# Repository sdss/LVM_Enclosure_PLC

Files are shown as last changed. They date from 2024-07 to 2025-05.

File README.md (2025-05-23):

# LVM_Enclosure_PLC
LVM enclosure PLC code and documentation. There is also an HVAC Modbus configuration file that details the commands to the HVAC system attached to the north side of the attic.

# Where to start?
Generally, look in the Documentation Directory.

# If changes are made

If PLC code is changed then one must
- Upload a new version of the code to PLC code
- Change PLC code.pdf in Documentaiton
- Change PLC Variables.xlsx in Documentation
- Make new state diagrams and upload to PLC State Diagrams

If Hardware is changed
- Change the Altium Schematics
- Upload new PDFs to Documentation

# Branches
* Main: Code deployed on the PLC.

PLC code has been written using Do-more Designer 2.9.

Documentation has the state diagrams for the different subsystems and a variable spreadsheet explaining the variables used in the code.

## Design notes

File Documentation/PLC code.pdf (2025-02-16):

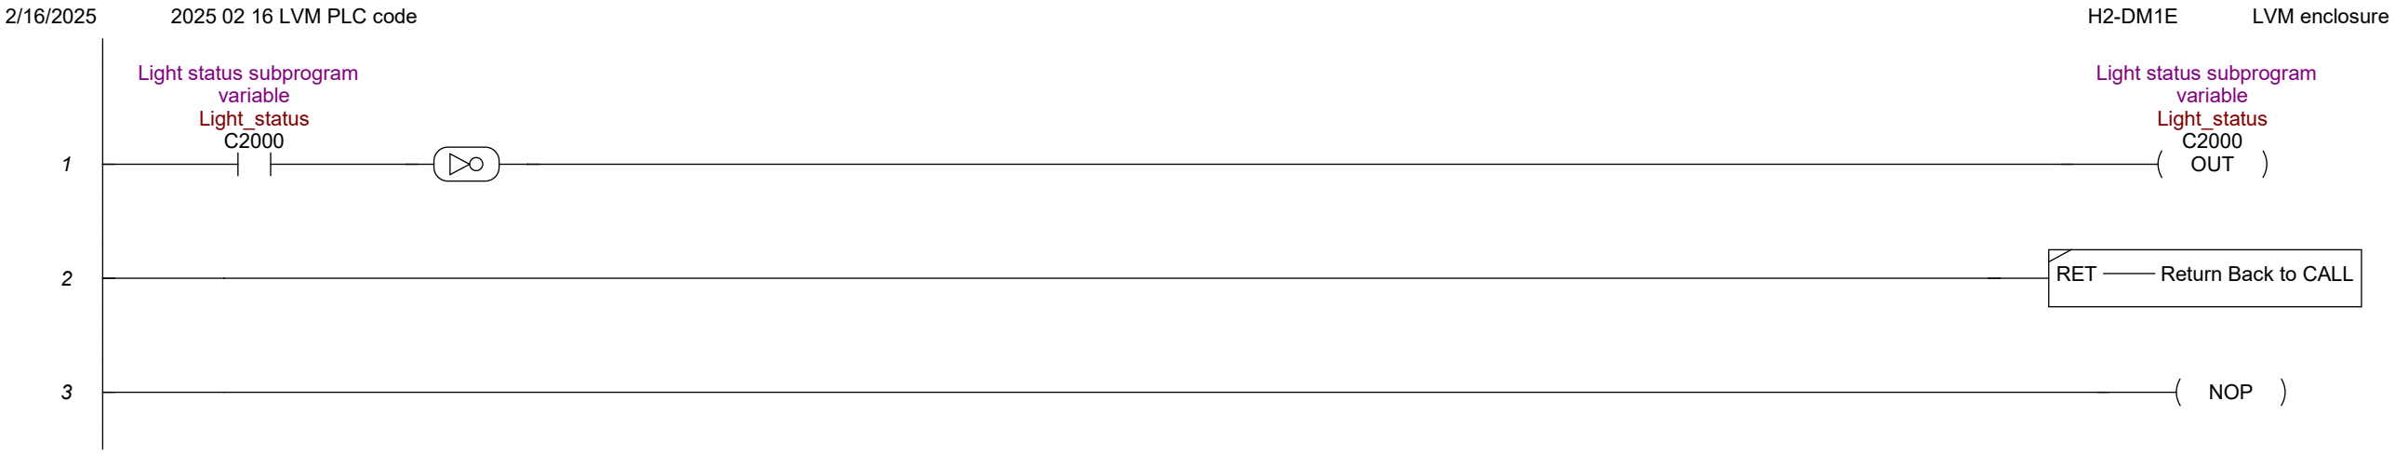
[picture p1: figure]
Light status subprogram variable Light_status C2000; OUT; RET; Return Back to CALL; 3 NOP

2/16/2025 | 2025 02 16 LVM PLC code | H2-DM1E | LVM enclosure
Page 1 | Lights

2/16/2025 | 2025 02 16 LVM PLC code | H2-DM1E | LVM enclosure 1

$FirstScan
ST0

$On
ST1 | INIT | Initialize Data
Start | End | Value
Overcurrent_lim | 75
Dome_move_tout | 165000
curr_delay_val | 2000
Dome_enable

0
Motor_dir

1
HB_error_count

0
Remote_estop

0
Remote_estop_rel

0
date.Date | $Now.Date
date.Time | $Now.Time
UTC | $UTC
C0

0
Rain_mod

0
Rain_el_time

0
No_rain_cdown

0
Drive_speed_a | 100
Drive_speed_b | 70
Roof_logic_sel

1
Rolloff_lout Drive_err_rst_mo

0
Tout_open | 81000
Tout_open_aprch | 37000
Topen_apr | 28000
Tclose | 74000
Tout_close_apr | 44000

Control room lights current sensor input
Local S1:iPT8
Ctl_lights_in
X24
CALL | Call Subroutine
Subroutine | Lights
Optional Input Parameters # | Input Value | Into Subroutine | Count 1 | Ctl_lights_out | Light_status | 1
Optional Output Parameters # | Out of Subroutine | Into | Count 1 | Light_status | Ctl_lights_out | 1

Utilities room lights current sensor input
Local S1:iPT9
Utl_room_in
X25
CALL | Call Subroutine
Subroutine | Lights
Optional Input Parameters # | Input Value | Into Subroutine | Count 1 | Utl_lights_out | Light_status | 1
Optional Output Parameters # | Out of Subroutine | Into | Count 1 | Light_status | Utl_lights_out | 1
Page 2 | $Main

Spectrograph room lights
current sensor input
Local S1:iPT10
Spec_lights_in
X26
CALL | Call Subroutine
Subroutine | Lights
Optional Input Parameters # | Input Value | Into Subroutine | Count 1 | Spec_lights_out | Light_status | 1
Optional Output Parameters # Out of Subroutine | Into | Count 1 | Light_status | Spec_lights_out | 1

Mezzanine lights current
sensor input
Local S1:iPT11
Mze_lights_in
X27
CALL | Call Subroutine
Subroutine | Lights
Optional Input Parameters # | Input Value | Into Subroutine | Count 1 | Mze_lights_out | Light_status | 1
Optional Output Parameters # Out of Subroutine | Into | Count 1 | Light_status | Mze_lights_out | 1

Platform white light
current sensor input
Local S1:iPT12
Plat_Wlights_in
X28
CALL | Call Subroutine
Subroutine | Lights
Optional Input Parameters # | Input Value | Into Subroutine | Count 1 Plat_Wlight_out | Light_status | 1
Optional Output Parameters # Out of Subroutine | Into | Count 1 | Light_status | Plat_Wlight_out | 1

Platform red light current sensor input
Local S1:iPT13
Plat_Rlights_in
X29
CALL | Call Subroutine
Subroutine | Lights
Optional Input Parameters # | Input Value | Into Subroutine | Count 1 | Plat_Rlight_out | Light_status | 1
Optional Output Parameters # Out of Subroutine | Into | Count 1 | Light_status | Plat_Rlight_out | 1

Read GS3 drive Elements using the cpu rs-232 port

Page 3 | $Main

Modbus Address 4… + offset value entered below

Modbus Address 4… + offset value entered below

Copy the encoder counts output to MHR150

- If motor is not moving, send data every minute.
- If motor is moving, send data every second.

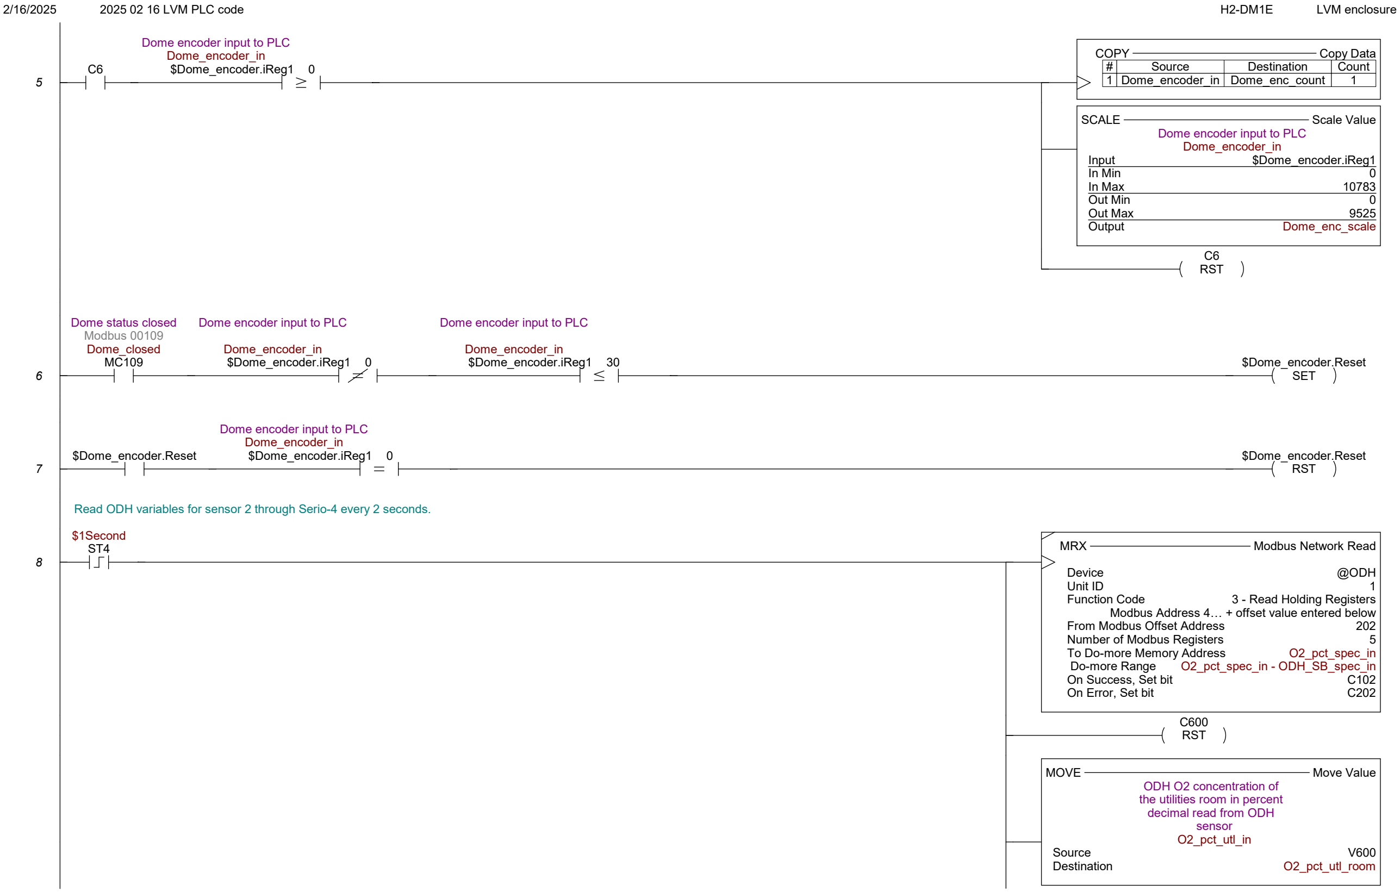
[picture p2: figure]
Dome encoder input to PLC Dome_encoder_in $Dome_encoder.iReg1 0; COPY; Copy Data; Source; Destination; Count; 1 Dome_encoder_in Dome_enc_count; SCALE; Scale Value; Dome encoder input to PLC Dome_encoder_in; Input; $Dome_encoder.iReg1; In Min; In Max; Out Min; Out Max; Output; Dome_enc_scale; RST; Dome status closed Modbus 00109 Dome_closed MC109; Dome encoder input to PLC; Dome_encoder_in $Dome_encoder.iReg1 0; Dome_encoder_in $Dome_encoder.iReg1 30; SET; $Dome_encoder.Reset; $1Second; MRX; Modbus Network Read; Device; @ODH; Unit ID; Function Code; 3 - Read Holding Registers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

Read ODH variables for sensor 2 through Serio-4 every 2 seconds.

Modbus Address 4… + offset value entered below

Page 5 | $Main

MOVE | Move Value
| ODH error code utilities
| room read from ODH sensor
ODH_EC_utl_in
Source | V603
Destination | ODH_EC_utl_room
MOVE | Move Value
| ODH status byte utilities
room, read from ODH
sensor
ODH_SB_utl_in
Source | V604
Destination | ODH_SB_utl_room

9

Read ODH variables for sensor 1 through Serio-4 every 2 seconds.

$1Second
ST4 | MRX | Modbus Network Read
| Device | @ODH
| Unit ID | 1
| Function Code
Modbus Address 4… + offset value entered below
| | 3 - Read Holding Registers
| From Modbus Offset Address | 102
| Number of Modbus Registers | 5
To Do-more Memory Address
| Do-more Range | O2_pct_utl_in - ODH_SB_utl_in O2_pct_utl_in
| On Success, Set bit | C103
| On Error, Set bit | C203

SET

C600

MOVE | Move Value
| ODH O2 concentration of
| the spectrograph room in
| percent decimal, read from
| ODH sensor
| O2_pct_spec_in
Source | V605
Destination | O2_pct_spec_room
MOVE | Move Value
| ODH error code
| spectrograph room, read
| from ODH sensor
| ODH_EC_spec_in
Source | V608
Destination | ODH_EC_spec_room
MOVE | Move Value
| ODH status byte
| spectrograph room, read
| from ODH sensor
| ODH_SB_spec_in
Source | V609
Destination | ODH_SB_spec_room
Page 6 | $Main

10

$1Second
ST4
MATH | Calculate Expression
| Modbus 40700
| Rain_el_time
Result | MHR700
Expression TRUNC(Rain_elapsd_time.Acc / 1000)
MATH | Calculate Expression
| Countdown from 15 min with
no rain
| Modbus 40701
| No_rain_cdown
Result | MHR701
Expression TRUNC(Rain_time.Acc / 1000)

11

$On
ST1

Dome movement mode
selector: selects between
normal operation and
overcurrent only mode.
Modbus 00099
Dome_move_sel
MC99
RUN | Run Program

Overcurrent Drive mode

Program | Drive_overcur
HALT | Halt Program or Task
Code Block | Drive

Dome movement mode
selector: selects between
normal operation and
overcurrent only mode.
Modbus 00099
Dome_move_sel
MC99
RUN | Run Program
Program | Drive
HALT | Halt Program or Task
Overcurrent Drive mode
Code Block Drive_overcur

12

$On
ST1
RUN | Run Program
Rain sensor program
Program | Rain
RUN | Run Program
Program | NTP
RUN | Run Program
Program | Heartbeat
Page 7 | $Main

Optional Output Parameters # Out of Subroutine | Into | Count 1 | Light_status | Ctl_lights_out | 1

18

Modbus utilities room lights toggle
Modbus 00236
UTL_room_tog
MC236
CALL | Call Subroutine
Subroutine | Lights
Optional Input Parameters # | Input Value | Into Subroutine | Count 1 Utl_lights_out | Light_status | 1
Optional Output Parameters # Out of Subroutine | Into | Count 1 | Light_status | Utl_lights_out | 1

RST

Modbus utilities room lights
toggle
Modbus 00236
UTL_room_tog
MC236

19

Utilities room lights current sensor input
Local S1:iPT9
Utl_room_in
X25
OUT

Modbus utilities room lights status
Modbus 00336
UTL_room_stat
MC336

20

Modbus Spectrograph room
lights toggle
Modbus 00237
Spec_room_tog
MC237
CALL | Call Subroutine
Subroutine | Lights
Optional Input Parameters # | Input Value | Into Subroutine | Count 1 Spec_lights_out | Light_status | 1
Optional Output Parameters # Out of Subroutine | Into | Count 1 | Light_status | Spec_lights_out | 1
COPY | Copy Data # | Source | Destination | Count 1 | $UTC | UTC | 1

RST

C0

RST

Modbus Spectrograph room
lights toggle
Modbus 00237
Spec_room_tog
MC237
Page 9 | $Main

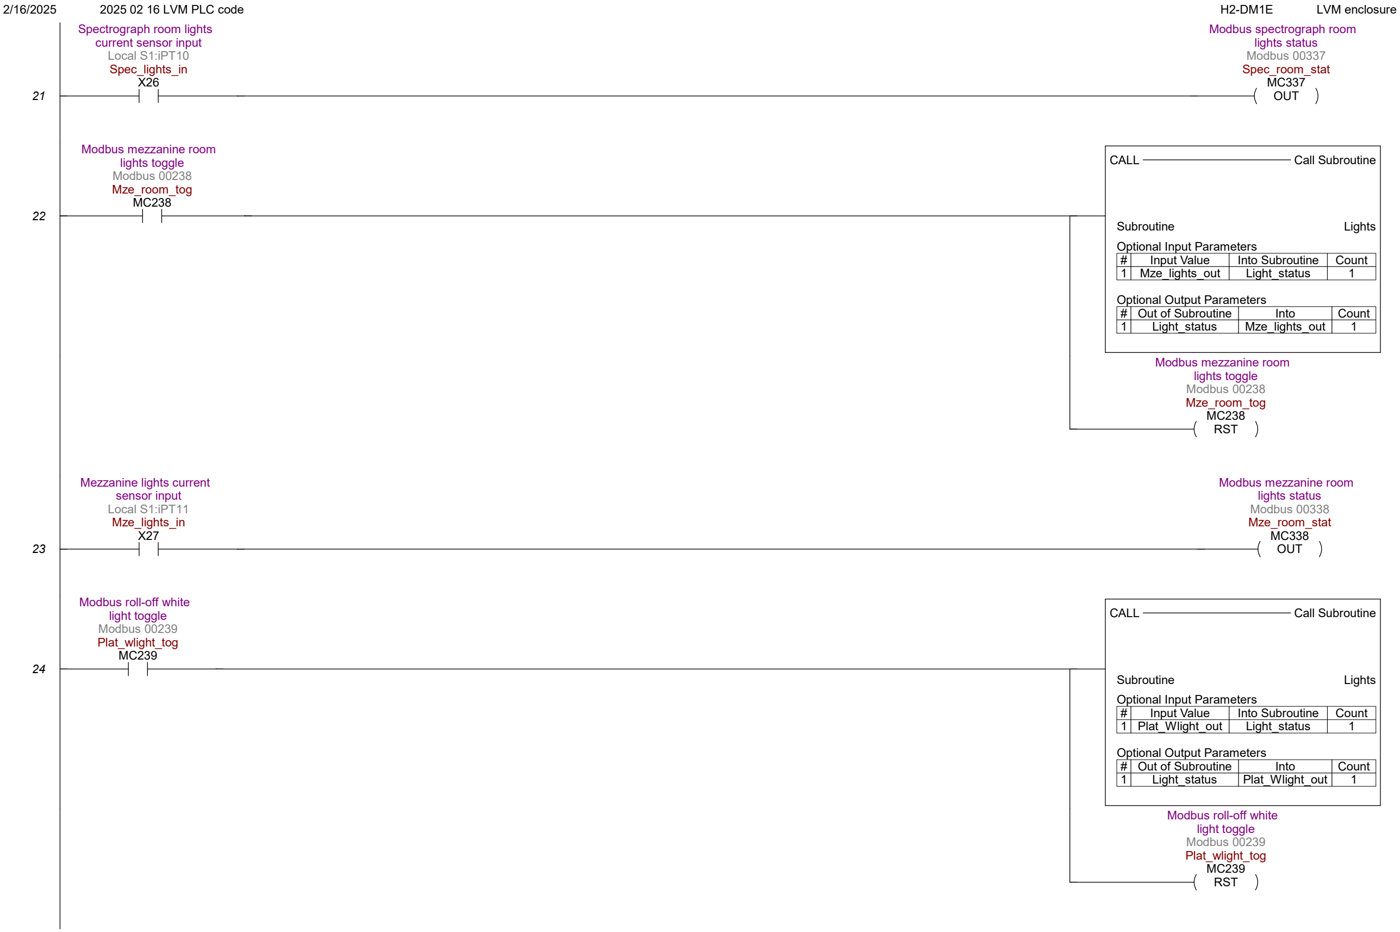
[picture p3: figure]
Spectrograph room lights current sensor input Local S1:iPT10 Spec_lights_in X26; OUT; Modbus spectrograph room lights status Modbus 00337 Spec_room_stat MC337; Modbus mezzanine room lights toggle Modbus 00238 Mze_room_tog MC238; CALL; Call Subroutine; Subroutine; Lights; Optional Input Parameters #; Input Value; Into Subroutine; Count 1 Mze_lights_out; Light_status; RST; Mezzanine lights current sensor input Local S1:iPT11 Mze_lights_in X27; Modbus mezzanine room lights status Modbus 00338 Mze_room_stat MC338; Modbus roll-off white light toggle Modbus 00239 Plat_wlight_tog MC239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

Optional Output Parameters # Out of Subroutine | Into | Count 1 | Light_status | Mze_lights_out | 1
Optional Output Parameters # Out of Subroutine | Into | Count 1 | Light_status | Plat_Wlight_out | 1
Page 10 | $Main

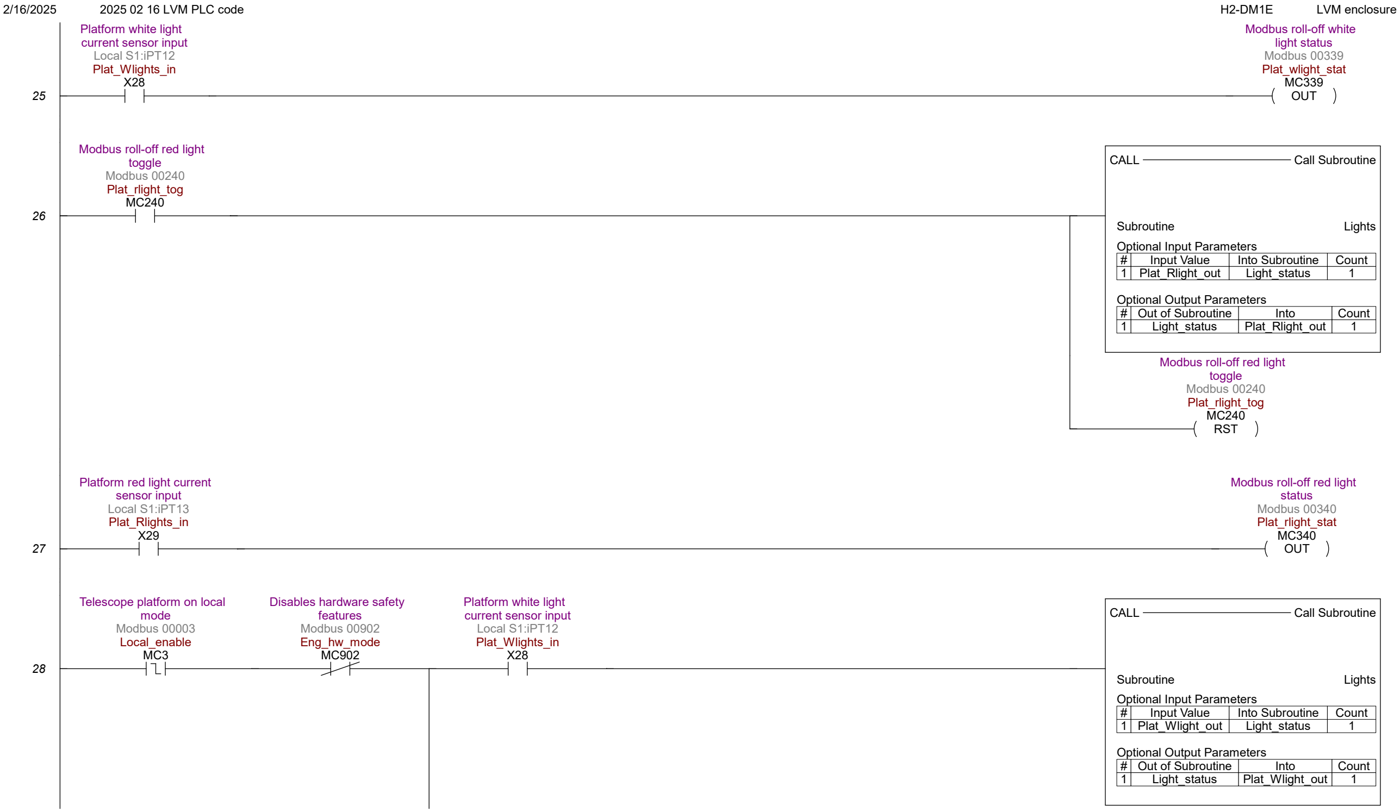
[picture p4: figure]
Platform white light current sensor input Local S1:iPT12 Plat_Wlights_in X28; OUT; Modbus roll-off white light status Modbus 00339 Plat_wlight_stat MC339; Modbus roll-off red light toggle Modbus 00240 Plat_rlight_tog MC240; CALL; Call Subroutine; Subroutine; Lights; Optional Input Parameters; Input Value; Into Subroutine; Count; 1 Plat_Rlight_out; Light_status; Optional Output Parameters; # Out of Subroutine; Into; Plat_Rlight_out; RST; Platform red light current sensor input Local S1:iPT13 Plat_Rlights_in X29; Modbus roll-off red light status Modbus 00340 Plat_rlight_stat MC340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

Page 11 | $Main

Page 12 | $Main

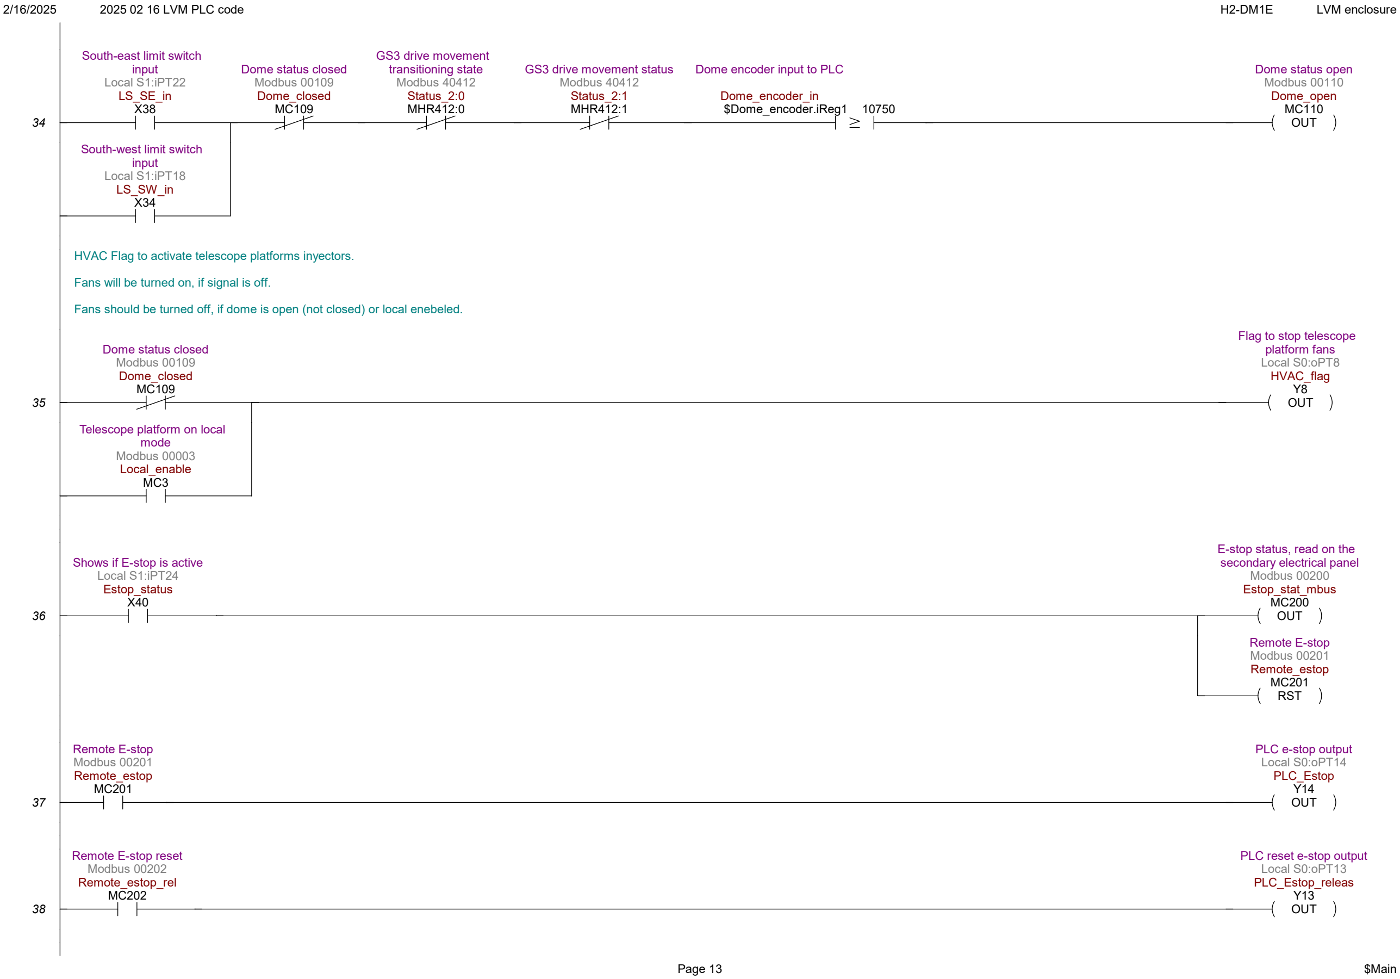
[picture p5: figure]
South-east limit switch input Local S1:iPT22 LS_SE_in X38; Dome status closed Modbus 00109 Dome_closed MC109; GS3 drive movement transitioning state Modbus 40412 Status_2:0 MHR412:0; GS3 drive movement status Modbus 40412 Status_2:1 MHR412:1; Dome encoder input to PLC; Dome_encoder_in $Dome_encoder.iReg1 10750; OUT; Dome status open Modbus 00110 Dome_open MC110; South-west limit switch input Local S1:iPT18 LS_SW_in X34; Flag to stop telescope platform fans Local S0:oPT8 HVAC_flag Y8; Telescope platform on local mode Modbus 00003 Local_enable MC3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

HVAC Flag to activate telescope platforms inyectors.

Fans will be turned on, if signal is off.

Fans should be turned off, if dome is open (not closed) or local enebeled.

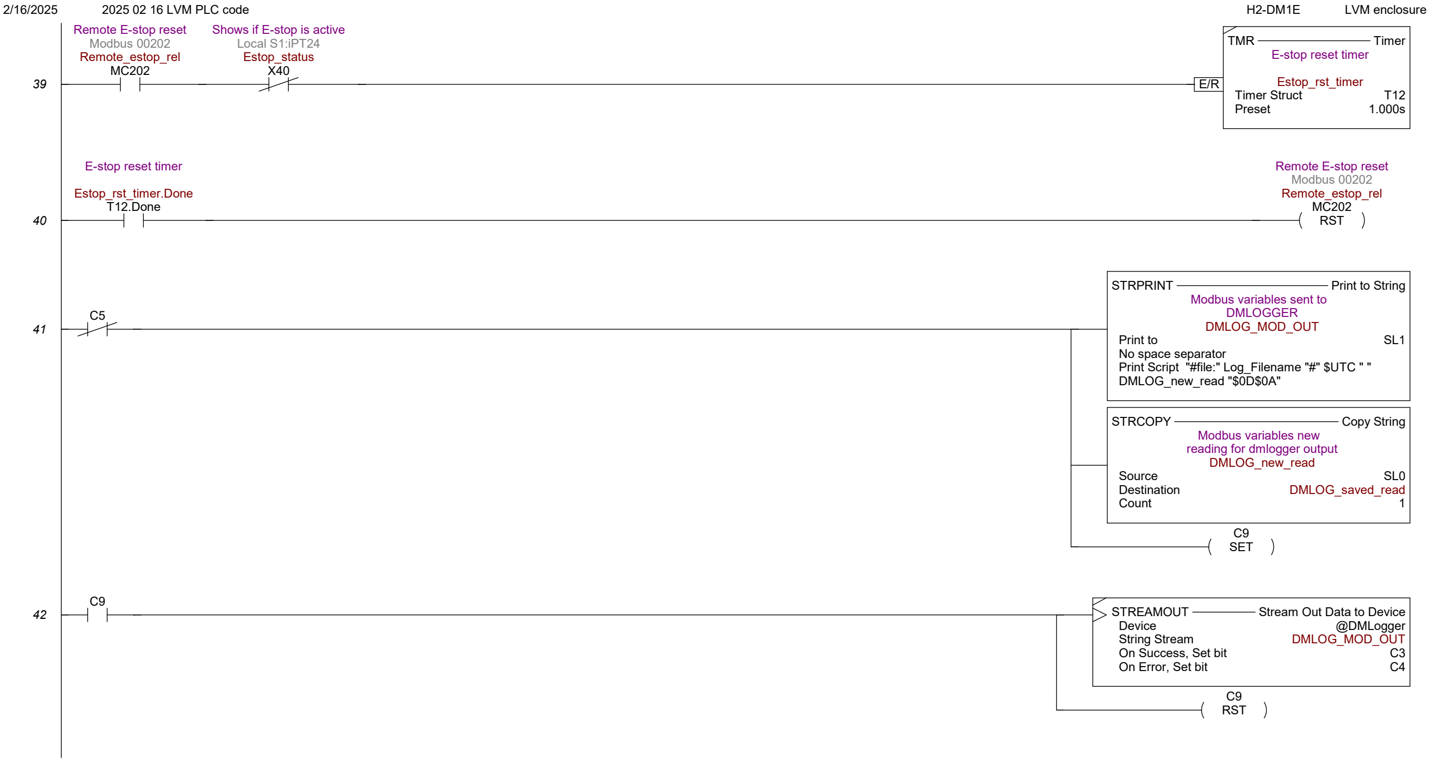
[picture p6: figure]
Remote E-stop reset Modbus 00202 Remote_estop_rel MC202; Shows if E-stop is active Local S1:iPT24 Estop_status X40; TMR; Timer; E-stop reset timer; Estop_rst_timer; Timer Struct; Preset; Estop_rst_timer.Done T12.Done; RST; STRPRINT; Print to String; Modbus variables sent to DMLOGGER DMLOG_MOD_OUT; Print to; No space separator; DMLOG_new_read "$0D$0A"; STRCOPY; Copy String; Modbus variables new reading for dmlogger output DMLOG_new_read; Source; Destination; DMLOG_saved_read; Count; SET; STREAMOUT; Stream Out Data to Device; Device; @DMLogger; String Stream; DMLOG_MOD_OUT; On Success, Set bit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

Print Script "#file:" Log_Filename "#" $UTC " "

Page 14 | $Main

43

$On
ST1
STRPRINT | Print to String
Modbus variables new
reading for dmlogger output DMLOG_new_read
Print to | SL0
Space separator inserted
Print Script Door_locked Door_closed Local_enable Dome_move_sel Dome_enable MC101 Motor_dir Dome_Tout_stat NE_lim_mod SE_lim_mod NW_lim_mod SW_lim_mod Dome_closed Dome_open Rolloff_lout Rolloff_error Estop_stat_mbus Remote_estop Remote_estop_rel CTL_room_tog UTL_room_tog Spec_room_tog Mze_room_tog Plat_wlight_tog Plat_rlight_tog CTL_room_stat UTL_room_stat Spec_room_stat Mze_room_stat Plat_wlight_stat Plat_rlight_stat HB_input HB_ACK HB_err_out Internet_disable Rain_mod Eng_hw_mode_mod Eng_sw_mode_mod Eng_hw_mode Eng_sw_mode Dome_enc_count Dome_speed Status_1 Status_2 VDF_des_freq VDF_out_freq Output_current VDF_output_volt VDF_output_RPM O2_pct_utl_room ODH_EC_utl_room rain_sen_in Brake_start
STRCMP | String Compare
Modbus variables to be
checked against at next
cycle
DMLOG_saved_read
First String | SL3
Case Sensitive Yes, upper/lower case are different
Set If Equal | C5
Second String or Text | DMLOG_new_read

44

$100ms
ST5 | DTCMP | Compare Date/Time
date
| First Date/Time | UDT0
| Second Date/Time | UDT1
| Compare Date Only
| Set if First Equals Second | C10
| EPOCH2DT | Convert Epoch to Date/Time
$UTC
| 1970 Epoch | DST21
| Date/Time | UDT1

45

C10 | EPOCH2DT | Convert Epoch to Date/Time
| | $UTC
| 1970 Epoch | DST21
| Date/Time | date
| | SET C11
Page 15 | $Main

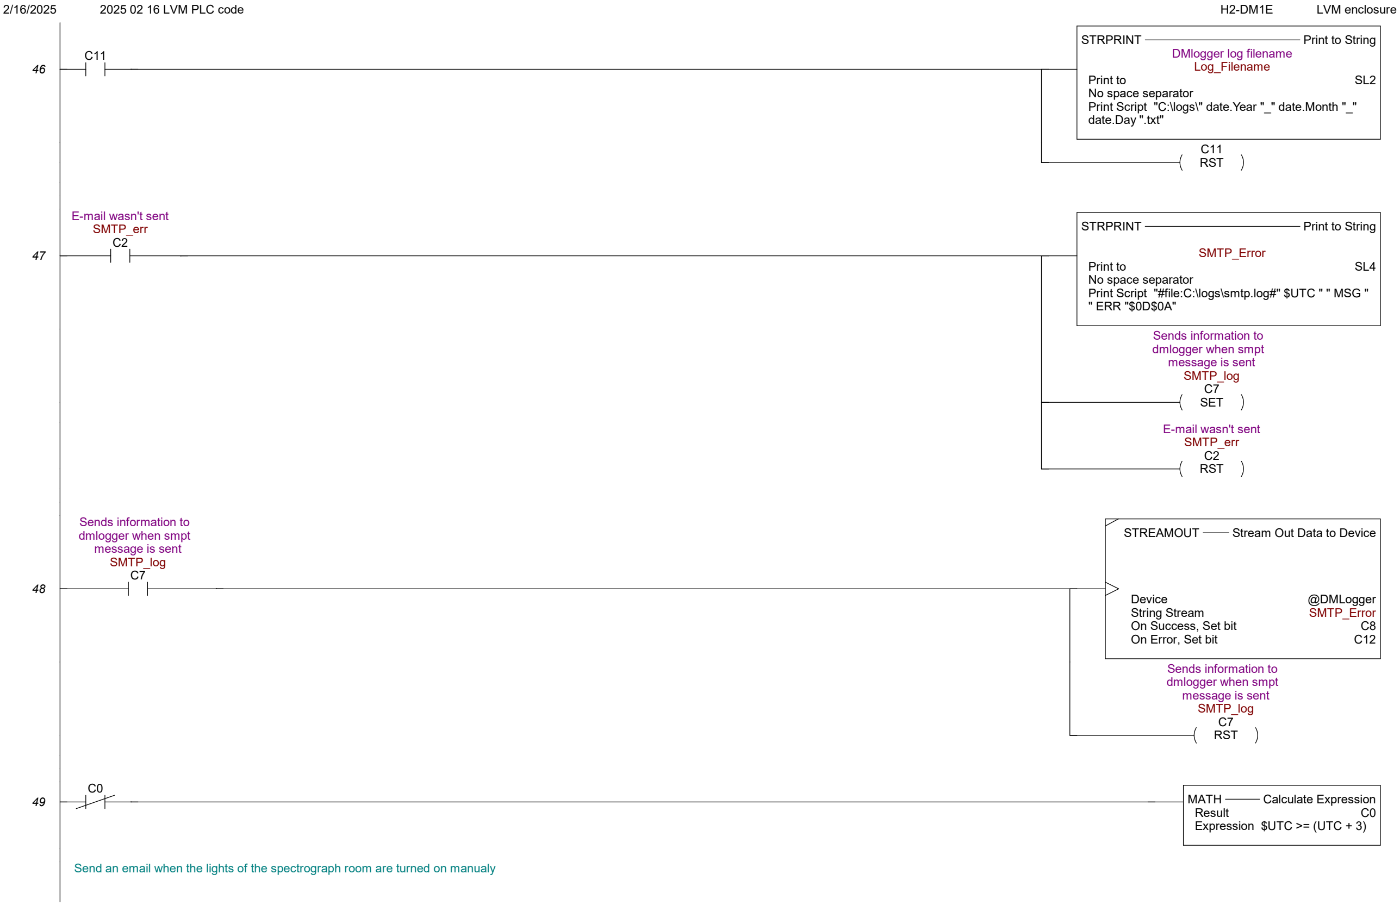
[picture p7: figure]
STRPRINT; Print to String; DMlogger log filename Log_Filename; Print to; No space separator; date.Day ".txt"; RST; E-mail wasn't sent SMTP_err C2; SMTP_Error; " ERR "$0D$0A"; SET; Sends information to dmlogger when smpt message is sent SMTP_log C7; STREAMOUT; Stream Out Data to Device; Device; @DMLogger; String Stream; On Success, Set bit; On Error, Set bit; MATH; Calculate Expression; Result; Expression $UTC >= (UTC + 3)

Print Script "C:\logs\" date.Year "_" date.Month "_"

Print Script "#file:C:\logs\smtp.log#" $UTC " " MSG "

Send an email when the lights of the spectrograph room are turned on manualy

Page 16 | $Main

50

Modbus Spectrograph room
lights toggle
Modbus 00237
Spec_room_tog
MC237

Spectrograph room lights
current sensor input
Local S1:iPT10
Spec_lights_in
X26 | C0

Disables software safety
features
Modbus 00903
Eng_sw_mode
MC903
EMAIL | Send EMail
SMTP Device | @LCO_smtp
To "lvm-critical@sdss.org"
Subject "Someone entered the Spectrograph room" No space separator
Message Print Script "Someone turned on the lights on the spectrograph room at " $Now.Day "/" $Now.Month "/" $Now.Year " " $Now.Hour ":" $Now.Minute " Local time."
On Success, Set bit | SMTP_success
On Error, Set bit | SMTP_err

51

Send an email when the lights of the spectrograph room are turned off manually

Modbus Spectrograph room
lights toggle
Modbus 00237
Spec_room_tog
MC237

Spectrograph room lights
current sensor input
Local S1:iPT10
Spec_lights_in
X26 | C0

Disables software safety
features
Modbus 00903
Eng_sw_mode
MC903
EMAIL | Send EMail
SMTP Device | @LCO_smtp
To "lvm-critical@sdss.org"
Subject "Someone left the Spectrograph room"
No space separator
Message Print Script "Someone turned off the lights on the spectrograph room at " $Now.Day "/" $Now.Month "/" $Now.Year " " $Now.Hour ":" $Now.Minute " Local time."
On Success, Set bit | SMTP_success
On Error, Set bit | SMTP_err

52

500 ms timer
timer_500ms.Done
T10.Done
E/R
TMR | Timer
500 ms timer
timer_500ms
Timer Struct | T10
Preset | 0.500s

53

Define day change for warning error changes.

For example, if the coin battery dies.

$1Minute
ST3 | COPY | Copy Data
# | Source | Destination Count

1 $Now.Day | V0 | 1

54

Send e-mail to lvm critical, if battery is low.

$BatteryLow
ST149 | STRPRINT | Print to String
| Print to | SS0
| Space separator inserted
Print Script "Coin cell battery has been depleted since " $Now.Day "/" $Now.Month "/" $Now.Year ". Please
| replace it with a 2032 coin cell battery."
Page 17 | $Main

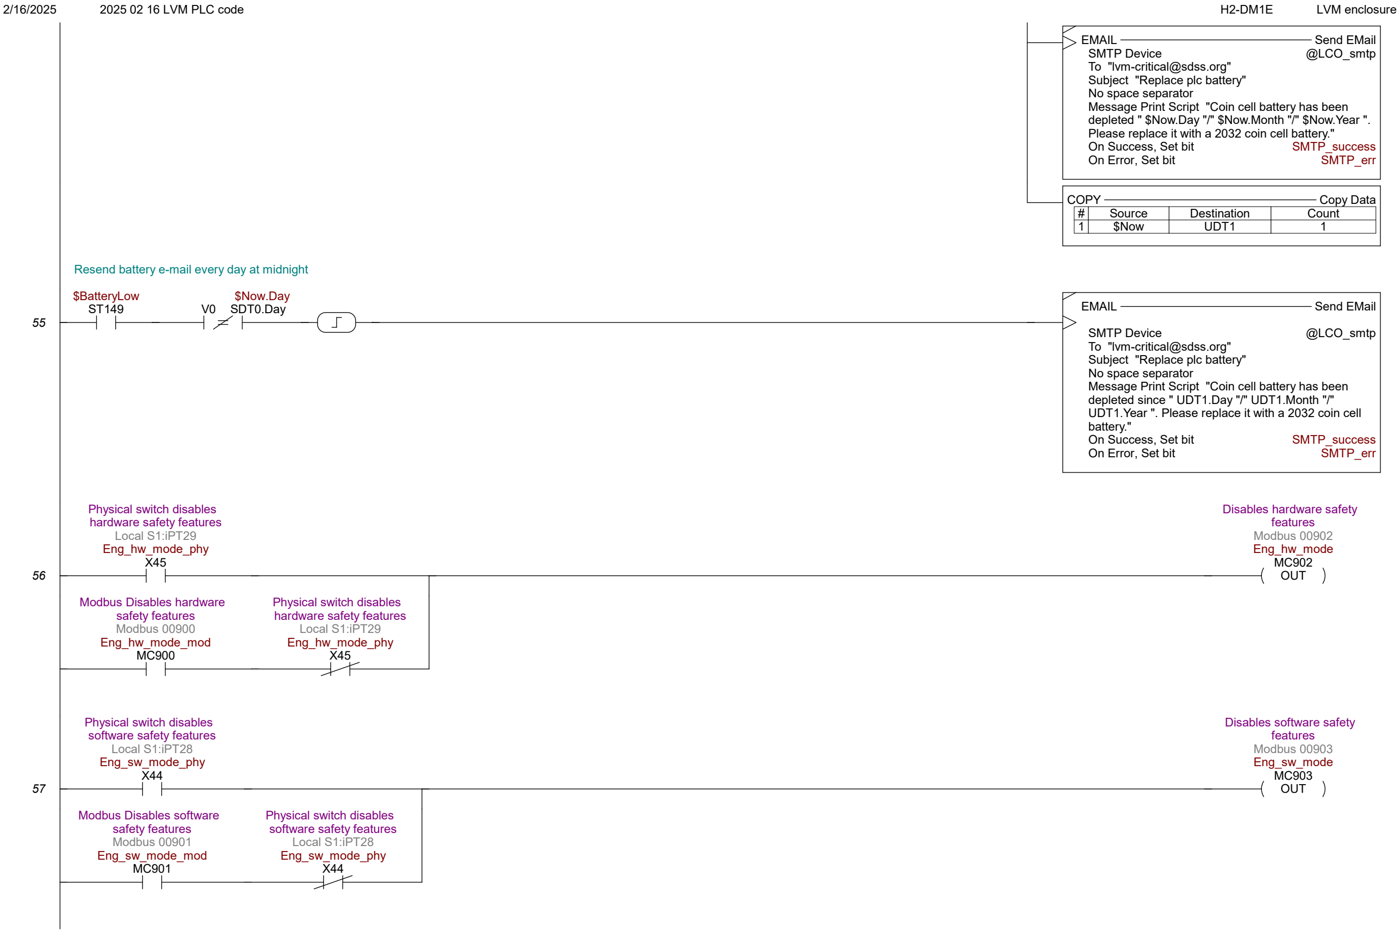
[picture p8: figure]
EMAIL; Send EMail; SMTP Device; @LCO_smtp; To "lvm-critical@sdss.org" Subject "Replace plc battery" No space separator; On Success, Set bit; SMTP_success; On Error, Set bit; SMTP_err; COPY; Copy Data #; Source; Destination; Count 1; $Now; UDT1; $BatteryLow ST149; $Now.Day; V0 SDT0.Day; battery."; Physical switch disables hardware safety features Local S1:iPT29 Eng_hw_mode_phy X45; OUT; Disables hardware safety features Modbus 00902 Eng_hw_mode MC902; Modbus Disables hardware safety features Modbus 00900 Eng_hw_mode_mod MC900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

Message Print Script "Coin cell battery has been depleted " $Now.Day "/" $Now.Month "/" $Now.Year ". Please replace it with a 2032 coin cell battery."

Resend battery e-mail every day at midnight

Message Print Script "Coin cell battery has been depleted since " UDT1.Day "/" UDT1.Month "/" UDT1.Year ". Please replace it with a 2032 coin cell

Page 18 | $Main

58

VDF output current
Modbus 40415
Output_current

Max motor current for the
las movement.

Max_VDF_Im
MHR415 D200
COPY | | | Copy Data
# | Source | Destination | Count

1 Output_current Max_VDF_Im | 1

59

Roll-off movement enable bit Modbus 00100
Dome_enable
MC100
COPY | Copy Data
# Source | Destination | Count

1 | 0 | Max_VDF_Im | 1

### 60 NOP

Page 19 | $Main

Stage; Drive idle stage Idle; Idle 2; Roll-off roof brake release Local S0:oPT9 Brake_start Y9; TMRDOWN; Down Timer; Brake_tmr; Timer Struct; Preset; Idle 3; GS3 drive movement transitioning state Modbus 40412 Status_2:0 MHR412:0; GS3 drive movement status Modbus 40412 Status_2:1 MHR412:1; Brake_tmr.Done T9.Done; RST; Idle 4; VDF desired frequency output Modbus 40413 VDF_des_freq MHR413 70; MWX; Modbus Network Write; Device; @IntSerModbusClient; Unit ID; Function Code; 6 - Write Single Register; To Modbus Offset Address; Constant; On Success, Set bit; On Error, Set bit; Idle 5; Select the direction of the motor.; On => Reverse direction (Open roll-off); GS3 drive direction Modbus 40412 Status_2:4 MHR412:4 0; Remote mode (local enable off) E-stop not triggered (Estop_status off)

Modbus Address 4… + offset value entered below

Off => Forward direction (Close roll-off)

Modbus Address 4… + offset value entered below

To move the roll off, the system has to be in:

Motor direction commanded has to agree with GS3 direction (Motor_dir == Status_2:4)

Page 20 | Drive_overcur

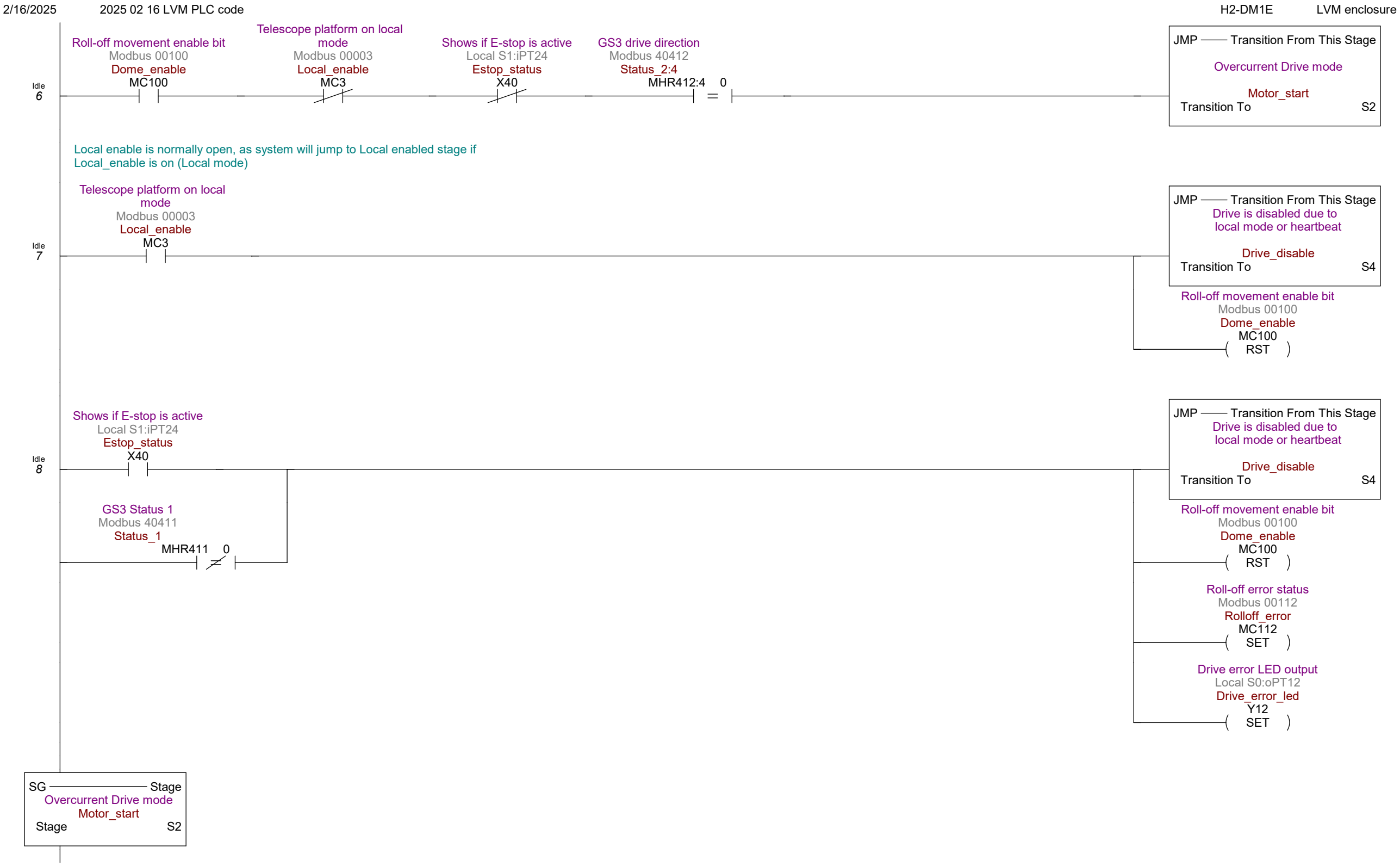
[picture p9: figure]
Idle 6; Roll-off movement enable bit Modbus 00100 Dome_enable MC100; Telescope platform on local mode Modbus 00003 Local_enable MC3; Shows if E-stop is active Local S1:iPT24 Estop_status X40; GS3 drive direction Modbus 40412 Status_2:4 MHR412:4 0; JMP; Transition From This Stage; Overcurrent Drive mode; Motor_start; Transition To; Idle 7; Local_enable is on (Local mode); Drive is disabled due to local mode or heartbeat; Drive_disable; RST; Idle 8; GS3 Status 1 Modbus 40411 Status_1 MHR411 0; SET; Roll-off error status Modbus 00112 Rolloff_error MC112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

Local enable is normally open, as system will jump to Local enabled stage if

Page 21 | Drive_overcur

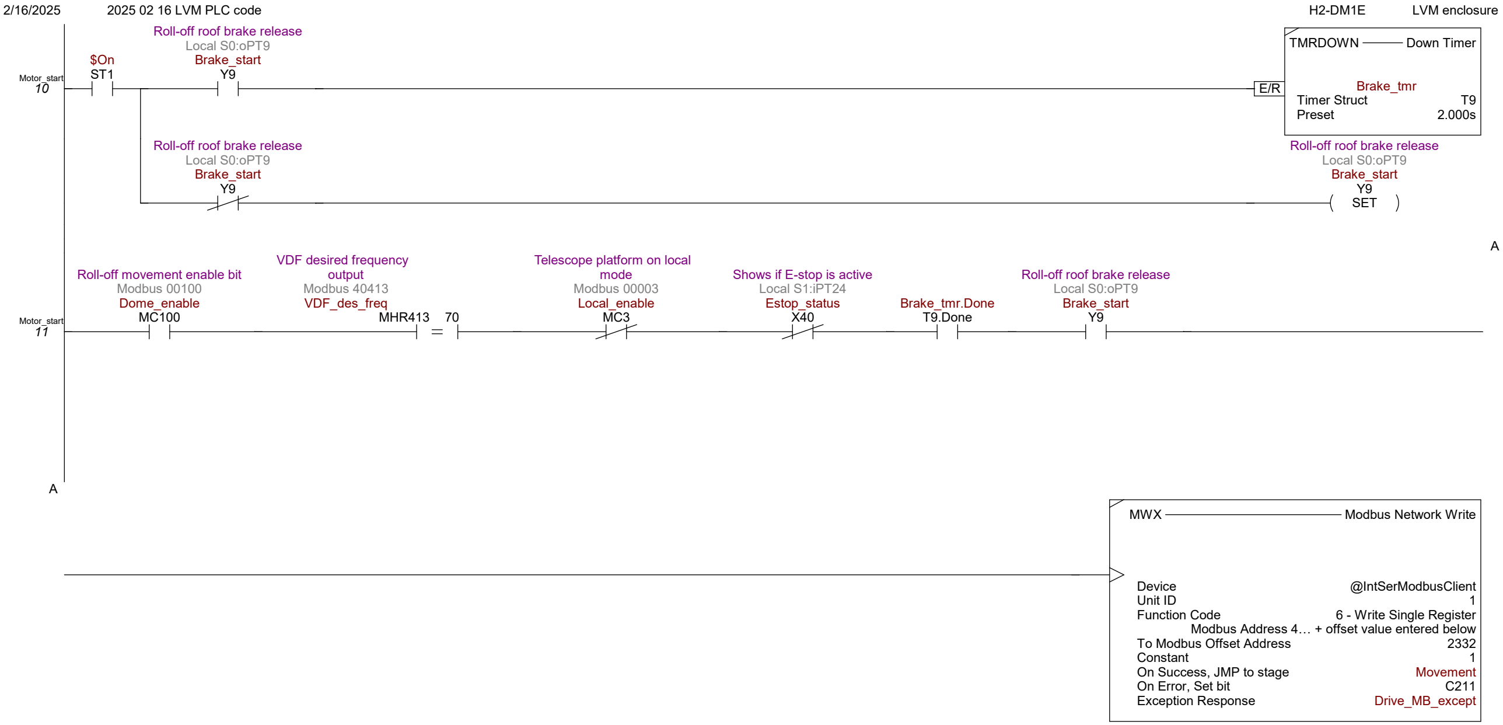
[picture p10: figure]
Motor_start 10; Roll-off roof brake release Local S0:oPT9 Brake_start Y9; TMRDOWN; Down Timer; Brake_tmr; Timer Struct; Preset; SET; Motor_start 11; Roll-off movement enable bit Modbus 00100 Dome_enable MC100; VDF desired frequency output Modbus 40413 VDF_des_freq MHR413 70; Telescope platform on local mode Modbus 00003 Local_enable MC3; Shows if E-stop is active Local S1:iPT24 Estop_status X40; Brake_tmr.Done T9.Done; MWX; Modbus Network Write; Device; @IntSerModbusClient; Unit ID; Function Code; 6 - Write Single Register; To Modbus Offset Address; Constant; On Success, JMP to stage; Movement; On Error, Set bit; Exception Response; Drive_MB_except

Modbus Address 4… + offset value entered below

Motor_start
12

Telescope platform on local mode
Modbus 00003
Local_enable
MC3
MWX | Modbus Network Write
Device | @IntSerModbusClient
Unit ID | 1
Function Code
Modbus Address 4… + offset value entered below
| 6 - Write Single Register
To Modbus Offset Address | 2332
Constant | 0
On Success, JMP to stage | lcout
On Error, Set bit | C211
Exception Response | Drive_MB_except
Page 22 | Drive_overcur

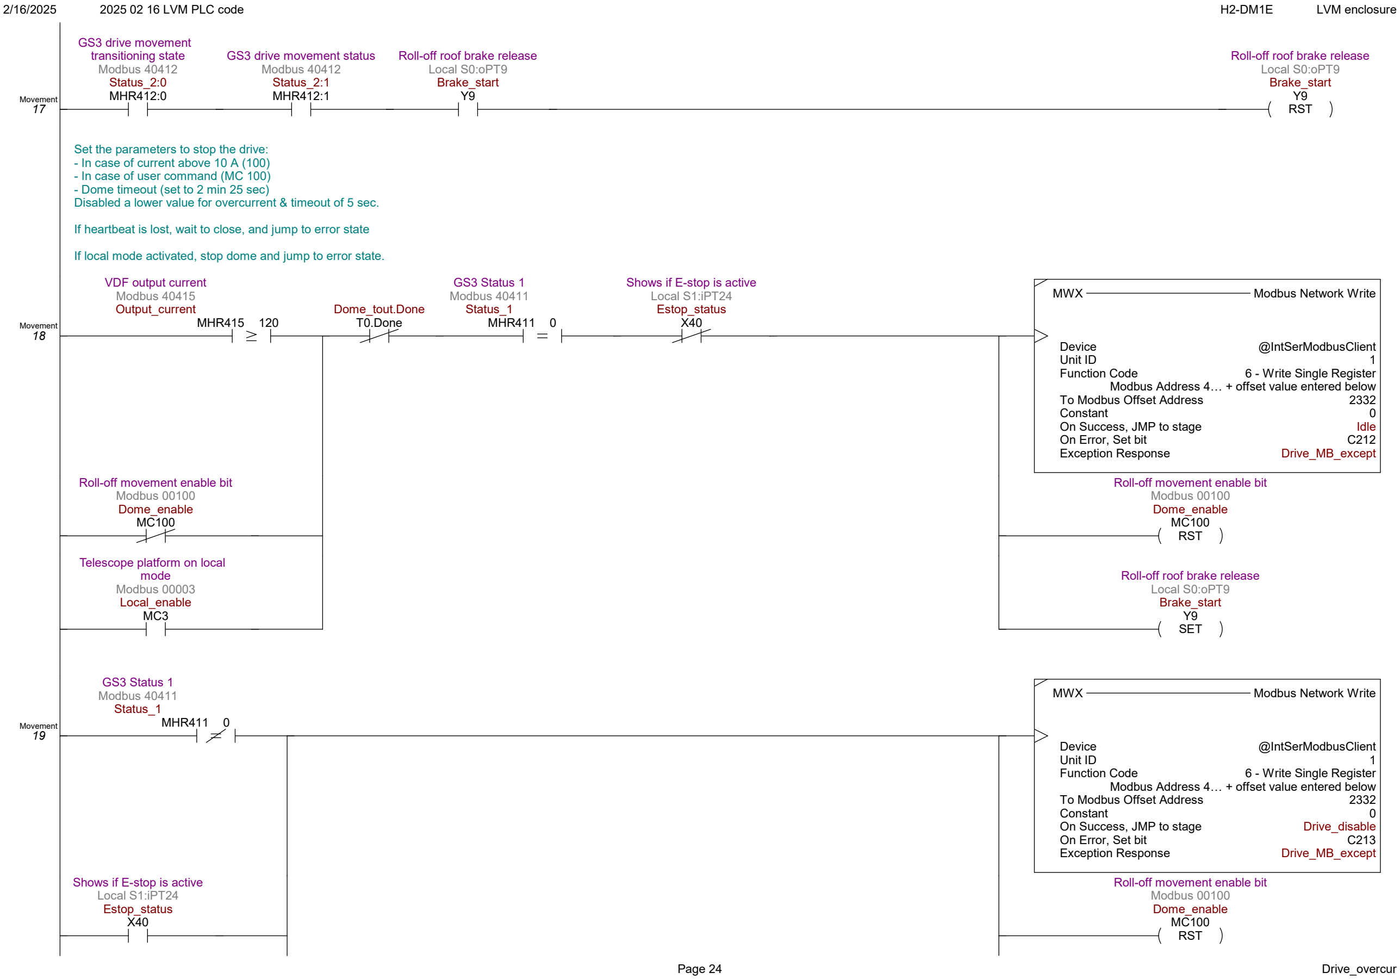
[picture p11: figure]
Movement 17; GS3 drive movement transitioning state Modbus 40412 Status_2:0 MHR412:0; GS3 drive movement status Modbus 40412 Status_2:1 MHR412:1; Roll-off roof brake release Local S0:oPT9 Brake_start Y9; RST; Movement 18; Set the parameters to stop the drive: - In case of current above 10 A (100) - In case of user command (MC 100) - Dome timeout (set to 2 min 25 sec); VDF output current Modbus 40415 Output_current; MHR415 120; Dome_tout.Done T0.Done; GS3 Status 1 Modbus 40411 Status_1 MHR411 0; Shows if E-stop is active Local S1:iPT24 Estop_status X40; MWX; Modbus Network Write; Device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

Disabled a lower value for overcurrent & timeout of 5 sec.

If heartbeat is lost, wait to close, and jump to error state

If local mode activated, stop dome and jump to error state.

Modbus Address 4… + offset value entered below

Modbus Address 4… + offset value entered below

Page 25 | Drive_overcur

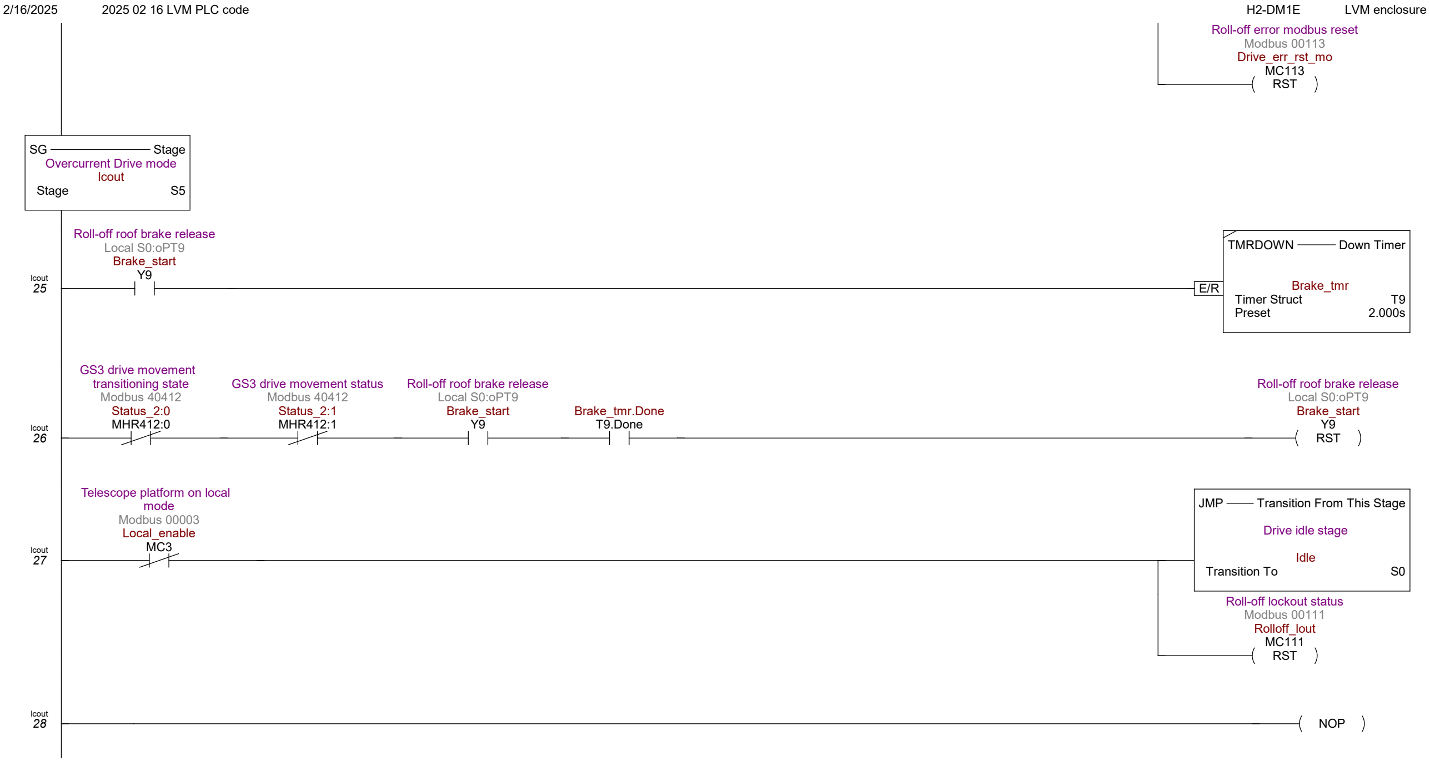
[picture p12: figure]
RST; Roll-off error modbus reset Modbus 00113 Drive_err_rst_mo MC113; Stage; Overcurrent Drive mode lcout; lcout 25; Roll-off roof brake release Local S0:oPT9 Brake_start Y9; TMRDOWN; Down Timer; Brake_tmr; Timer Struct; Preset; lcout 26; GS3 drive movement transitioning state Modbus 40412 Status_2:0 MHR412:0; GS3 drive movement status Modbus 40412 Status_2:1 MHR412:1; Brake_tmr.Done T9.Done; lcout 27; Telescope platform on local mode Modbus 00003 Local_enable MC3; JMP; Transition From This Stage; Drive idle stage; Idle; Transition To; Roll-off lockout status Modbus 00111 Rolloff_lout MC111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

Page 26 | Drive_overcur

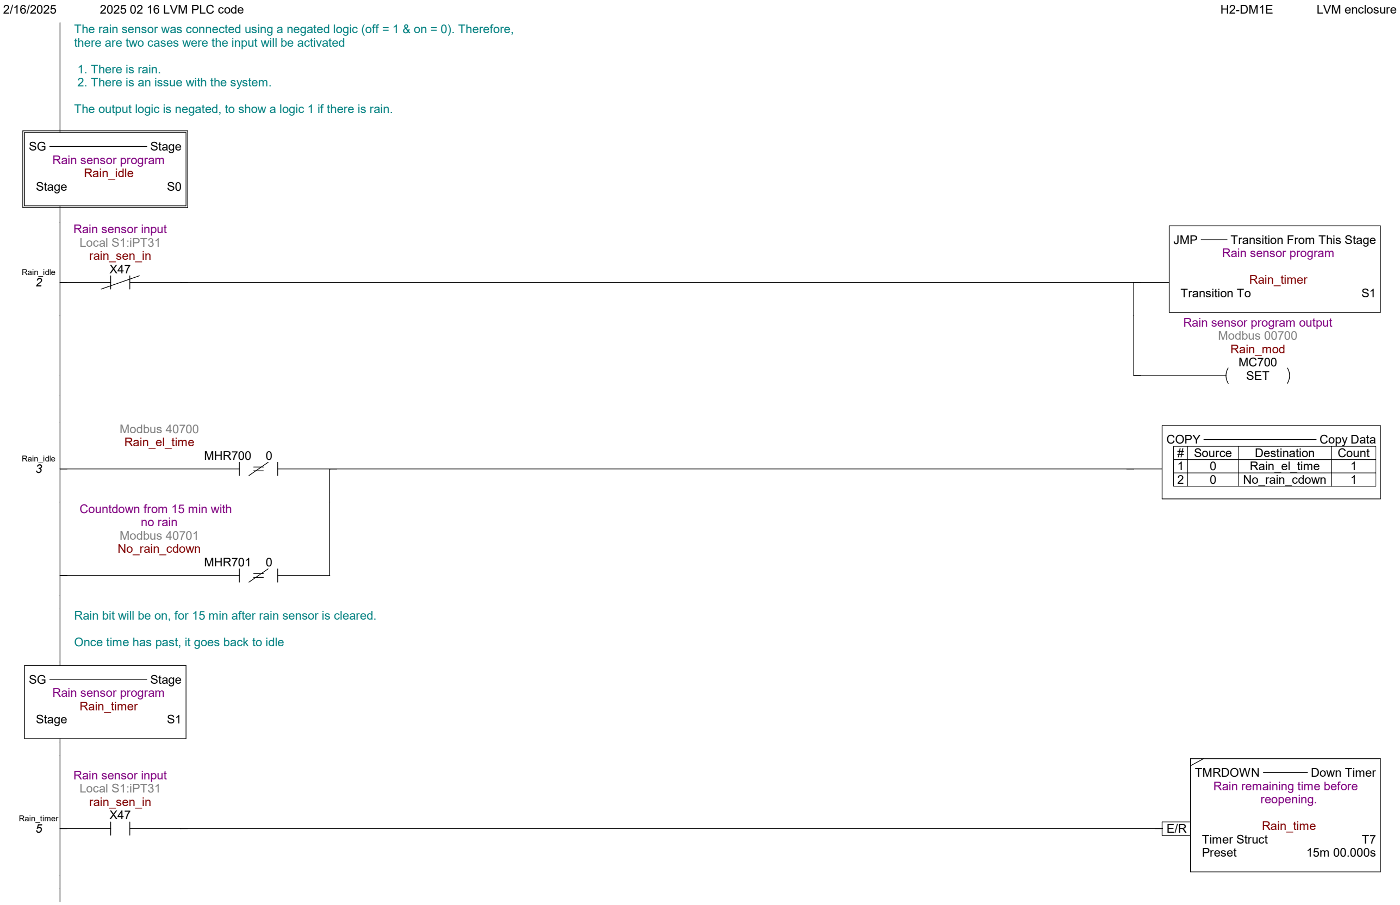
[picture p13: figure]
1. There is rain. 2. There is an issue with the system.; Stage; Rain sensor program Rain_idle; Rain_idle 2; Rain sensor input Local S1:iPT31 rain_sen_in X47; JMP; Transition From This Stage; Rain sensor program; Rain_timer; Transition To; SET; Rain sensor program output Modbus 00700 Rain_mod MC700; Rain_idle 3; Modbus 40700 Rain_el_time; MHR700 0; COPY; Copy Data; # Source; Destination; Count; Rain_el_time; No_rain_cdown; Countdown from 15 min with no rain Modbus 40701 No_rain_cdown; MHR701 0; Rain sensor program Rain_timer; Rain_timer 5; TMRDOWN; Down Timer; Rain remaining time before reopening.; Rain_time; Timer Struct; Preset

The rain sensor was connected using a negated logic (off = 1 & on = 0). Therefore, there are two cases were the input will be activated

The output logic is negated, to show a logic 1 if there is rain.

Rain bit will be on, for 15 min after rain sensor is cleared.

Once time has past, it goes back to idle

Page 27 | Rain

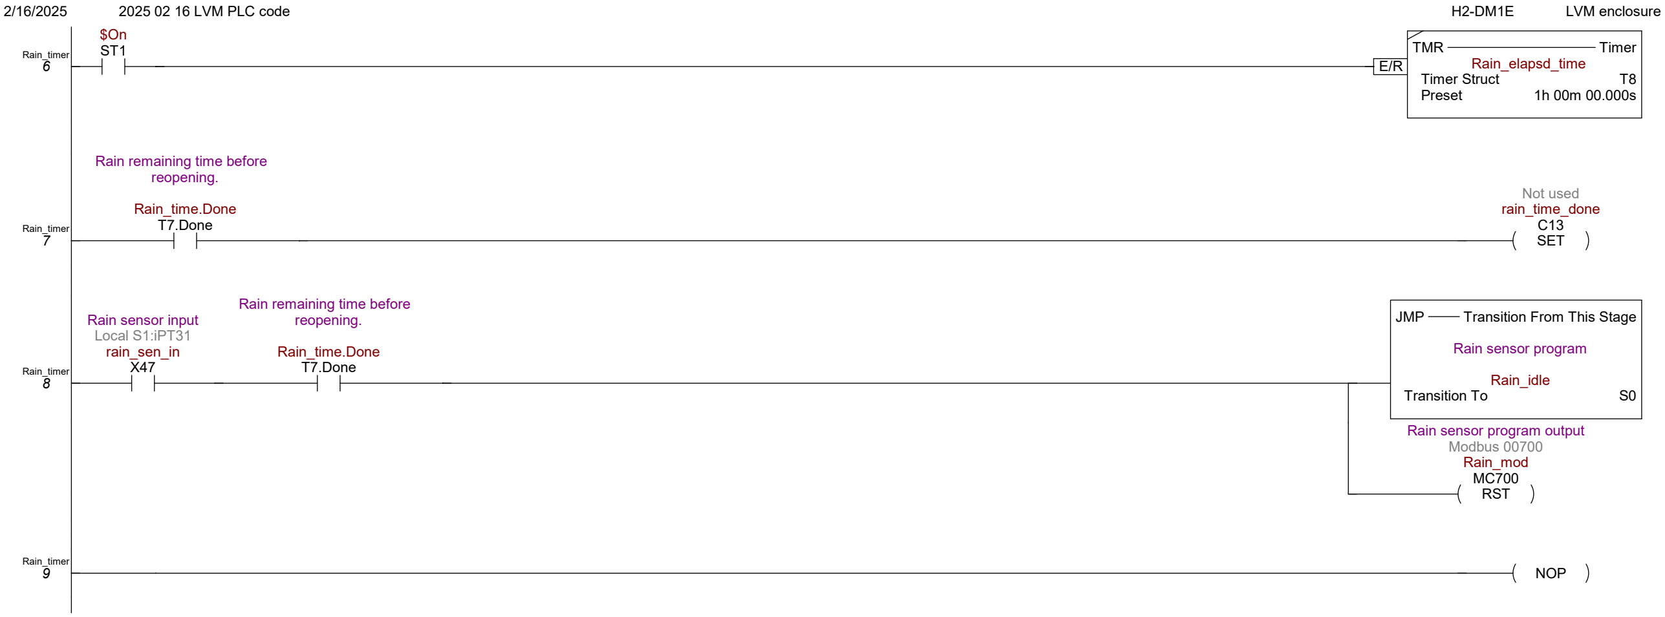
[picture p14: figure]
Rain_timer 6; TMR; Timer; Rain_elapsd_time; Timer Struct; Preset; Rain_timer 7; Rain remaining time before reopening.; Rain_time.Done T7.Done; SET; Not used rain_time_done C13; Rain_timer 8; Rain sensor input Local S1:iPT31 rain_sen_in X47; JMP; Transition From This Stage; Rain sensor program; Rain_idle; Transition To; RST; Rain sensor program output Modbus 00700 Rain_mod MC700; Rain_timer 9 NOP

Page 28 | Rain

Off => Forward direction (Close roll-off)

Modbus Address 4… + offset value entered below

Modbus Address 4… + offset value entered below

If it starts raining, system will automatically set drive direction to close.

Modbus Address 4… + offset value entered below

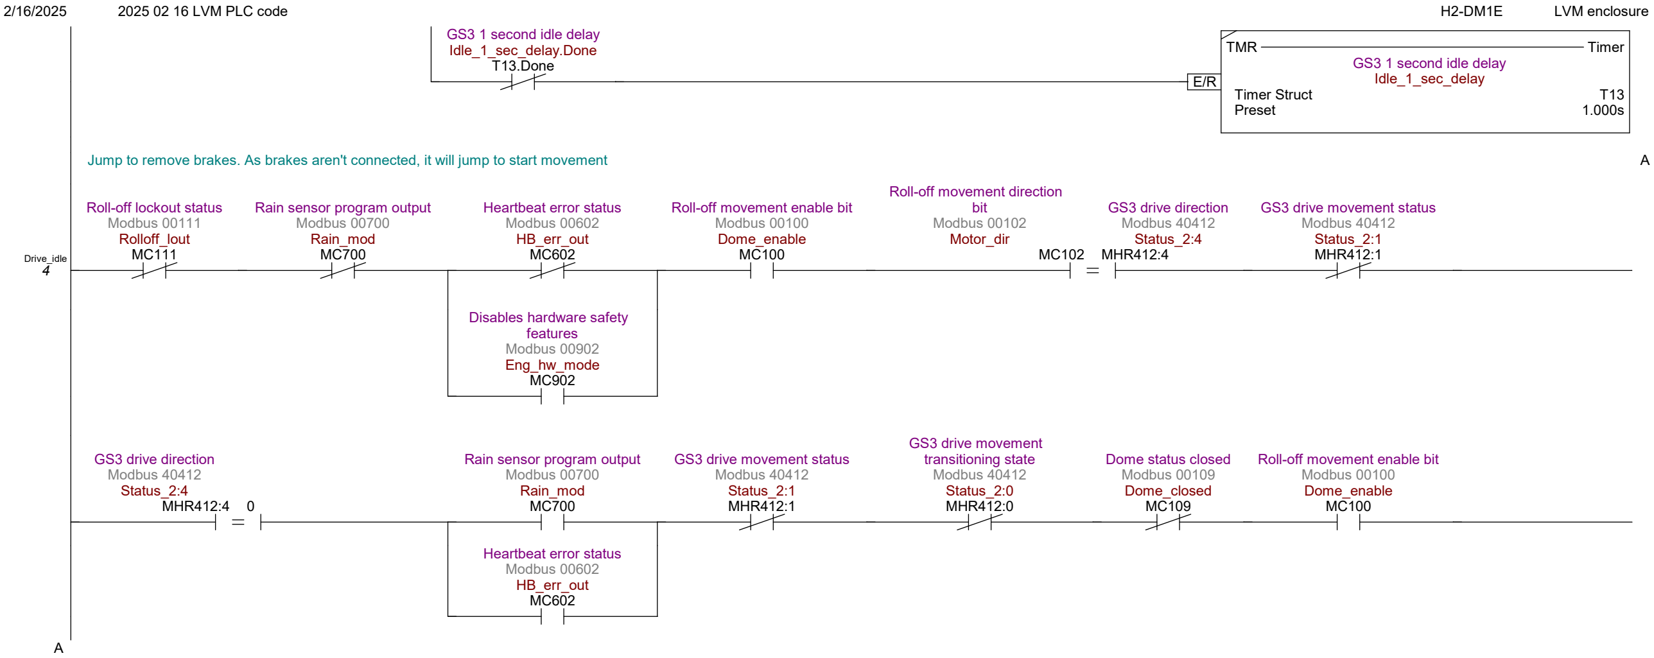
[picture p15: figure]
GS3 1 second idle delay Idle_1_sec_delay.Done T13.Done; TMR; Timer; GS3 1 second idle delay Idle_1_sec_delay; Timer Struct; Preset; Drive_idle 4; Roll-off lockout status Modbus 00111 Rolloff_lout MC111; Rain sensor program output Modbus 00700 Rain_mod MC700; Heartbeat error status Modbus 00602 HB_err_out MC602; Roll-off movement enable bit Modbus 00100 Dome_enable MC100; Roll-off movement direction bit Modbus 00102 Motor_dir; GS3 drive direction Modbus 40412 Status_2:4 MC102 MHR412:4; GS3 drive movement status Modbus 40412 Status_2:1 MHR412:1; Disables hardware safety features Modbus 00902 Eng_hw_mode MC902; GS3 drive direction Modbus 40412 Status_2:4 MHR412:4 0; GS3 drive movement transitioning state Modbus 40412 Status_2:0 MHR412:0; Dome status closed Modbus 00109 Dome_closed MC109

Jump to remove brakes. As brakes aren't connected, it will jump to start movement

GS3 drive movement
transitioning state
Modbus 40412
Status_2:0
MHR412:0

JMP Transition From This Stage

Rem_brakes
Transition To | S1

$Off
ST2

JMP Transition From This Stage

Start_movement
Transition To | S2
Page 30 | Drive

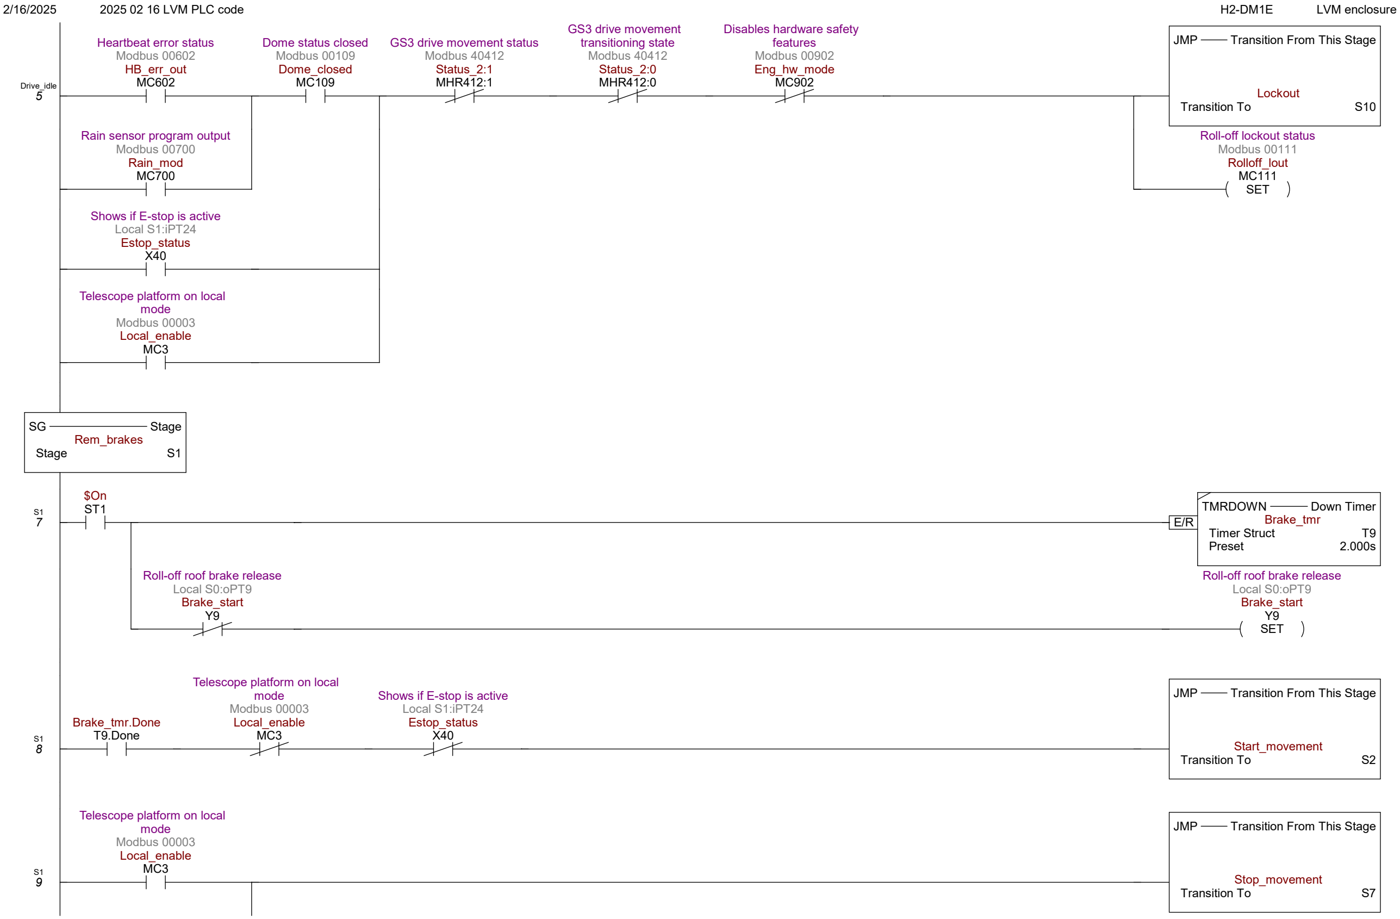
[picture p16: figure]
Drive_idle 5; Heartbeat error status Modbus 00602 HB_err_out MC602; Dome status closed Modbus 00109 Dome_closed MC109; GS3 drive movement status Modbus 40412 Status_2:1 MHR412:1; GS3 drive movement transitioning state Modbus 40412 Status_2:0 MHR412:0; Disables hardware safety features Modbus 00902 Eng_hw_mode MC902; JMP; Transition From This Stage; Lockout; Transition To; Rain sensor program output Modbus 00700 Rain_mod MC700; SET; Roll-off lockout status Modbus 00111 Rolloff_lout MC111; Shows if E-stop is active Local S1:iPT24 Estop_status X40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

Page 31 | Drive

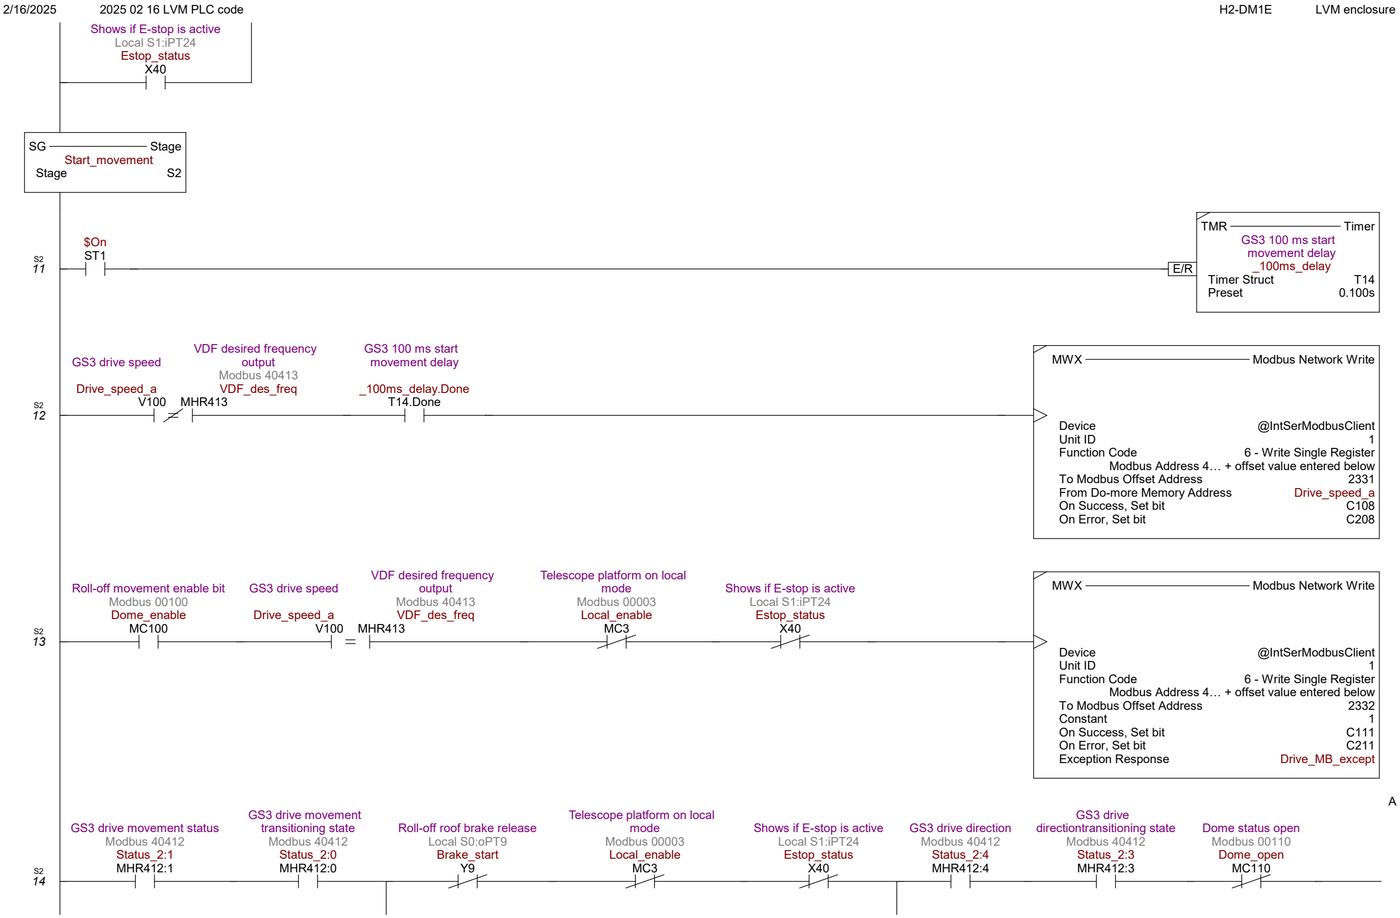
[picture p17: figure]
Shows if E-stop is active Local S1:iPT24 Estop_status X40; Stage; Start_movement; TMR; Timer; GS3 100 ms start movement delay _100ms_delay; Timer Struct; Preset; GS3 drive speed; Drive_speed_a; VDF desired frequency output Modbus 40413 VDF_des_freq V100 MHR413; GS3 100 ms start movement delay; _100ms_delay.Done T14.Done; MWX; Modbus Network Write; Device; @IntSerModbusClient; Unit ID; Function Code; 6 - Write Single Register; To Modbus Offset Address; From Do-more Memory Address; On Success, Set bit; On Error, Set bit; Roll-off movement enable bit Modbus 00100 Dome_enable MC100; Telescope platform on local mode Modbus 00003 Local_enable MC3; Constant; Exception Response; Drive_MB_except; GS3 drive movement status Modbus 40412 Status_2:1 MHR412:1; GS3 drive movement transitioning state Modbus 40412 Status_2:0 MHR412:0; Roll-off roof brake release Local S0:oPT9 Brake_start Y9; GS3 drive direction Modbus 40412 Status_2:4 MHR412:4; GS3 drive directiontransitioning state Modbus 40412 Status_2:3 MHR412:3; Dome status open Modbus 00110 Dome_open MC110

Modbus Address 4… + offset value entered below

Modbus Address 4… + offset value entered below

Page 32 | Drive

GS3 drive direction Modbus 40412 Status_2:4 MHR412:4; GS3 drive directiontransitioning state Modbus 40412 Status_2:3 MHR412:3; Dome status closed Modbus 00109 Dome_closed MC109; Roll-off roof brake release Local S0:oPT9 Brake_start Y9; JMP; Transition From This Stage; Open_roof; Transition To; Close_roof

RST

Roll-off roof brake release Local S0:oPT9
Brake_start
Y9

S2
15

Telescope platform on local mode
Modbus 00003
Local_enable
MC3

JMP Transition From This Stage

Stop_movement
Transition To | S7

GS3 drive
directiontransitioning state Modbus 40412
Status_2:3
MHR412:3

GS3 drive direction
Modbus 40412
Status_2:4
MHR412:4

Dome status open
Modbus 00110
Dome_open
MC110

GS3 drive
directiontransitioning state Modbus 40412
Status_2:3
MHR412:3

GS3 drive direction
Modbus 40412
Status_2:4
MHR412:4

Dome status closed
Modbus 00109
Dome_closed
MC109

Roll-off movement enable bit Modbus 00100
Dome_enable
MC100
Page 33 | Drive

Shows if E-stop is active
Local S1:iPT24
Estop_status
X40
SG | Stage
Open_roof
Stage | S3

Open_roof
17

$On
ST1
E/R
TMRDOWN | Down Timer
Dome_tout
Timer Struct | T0
Preset (ms) | Tout_open
COPY | | | Copy Data
# | Source | Destination | Count

1 Dome_tout.Acc Curr_tout_tmr | 1
2 Dome_tout.Acc Opn_tout_tmr | 1

Open_roof
18

South-east limit switch
input
Local S1:iPT22
LS_SE_in
X38
MWX | Modbus Network Write
Device | @IntSerModbusClient
Unit ID | 1
Function Code
Modbus Address 4… + offset value entered below
| 6 - Write Single Register
To Modbus Offset Address | 2331
From Do-more Memory Address | Drive_speed_b
On Success, JMP to stage | Open_aproach
On Error, Set bit | C208

South-west limit switch
input
Local S1:iPT18
LS_SW_in
X34

Dome encoder input to PLC
Dome_encoder_in

Open count mid limit
Open_count_mid
$Dome_encoder.iReg1 D100

Open_roof
19

Dome_tout.Done
T0.Done | JMP | Transition From This Stage
| | Stop_movement
Transition To | S7

GS3 Status 1
Modbus 40411
Status_1
MHR411 0
Page 34 | Drive

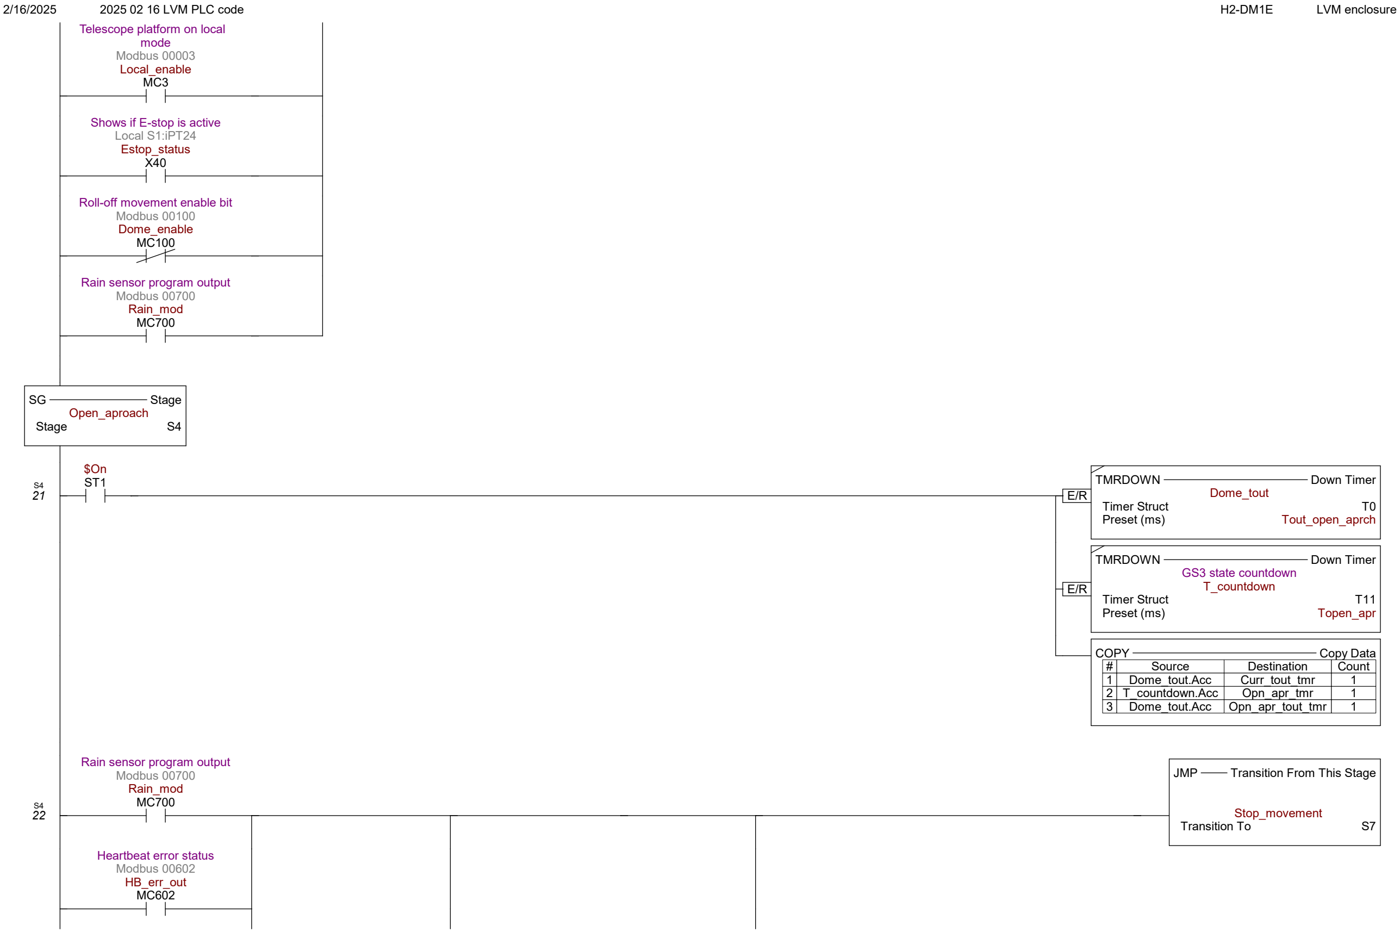
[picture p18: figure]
Telescope platform on local mode Modbus 00003 Local_enable MC3; Shows if E-stop is active Local S1:iPT24 Estop_status X40; Roll-off movement enable bit Modbus 00100 Dome_enable MC100; Rain sensor program output Modbus 00700 Rain_mod MC700; Stage; Open_aproach; TMRDOWN; Down Timer; Dome_tout; Timer Struct; Preset (ms); Tout_open_aprch; GS3 state countdown T_countdown; Topen_apr; JMP; Transition From This Stage; Stop_movement; Transition To; Heartbeat error status Modbus 00602 HB_err_out MC602

COPY | Copy Data # | Source | Destination | Count 1 | Dome_tout.Acc | Curr_tout_tmr | 1 2 T_countdown.Acc | Opn_apr_tmr | 1 3 | Dome_tout.Acc | Opn_apr_tout_tmr | 1
Page 35 | Drive

Dome_tout.Done T0.Done; Telescope platform on local mode Modbus 00003 Local_enable MC3; Shows if E-stop is active Local S1:iPT24 Estop_status X40; GS3 Status 1 Modbus 40411 Status_1; MHR411 0; Roll-off movement enable bit Modbus 00100 Dome_enable MC100; VDF output current Modbus 40415 Output_current; Motor current limit for end of movement; Im_limit; MHR415 D103; Dome encoder input to PLC; Dome_encoder_in; Open coun final limit; Open_count_final $Dome_encoder.iReg1 D101; GS3 state countdown; T_countdown.Done T11.Done; Dome encoder input to PLC Dome_encoder_in; Open coun final limit Open_count_final; $Dome_encoder.iReg1 D101; GS3 state countdown T_countdown.Done T11.Done; Stage; Close_roof; Close_roof 24; TMRDOWN; Down Timer; GS3 state countdown T_countdown; Timer Struct; Preset (ms); Tclose; COPY; Copy Data; Source; Destination Count; 1 T_countdown.Acc; Cls_tmr; Page 36; Drive

Close_roof
25

GS3 Status 1
Modbus 40411
Status_1
MHR411 0

JMP Transition From This Stage

Stop_movement
Transition To | S7

Telescope platform on local mode
Modbus 00003
Local_enable
MC3

Shows if E-stop is active
Local S1:iPT24
Estop_status
X40

Roll-off movement enable bit Modbus 00100
Dome_enable
MC100

Close_roof
26

GS3 state countdown
T_countdown.Done
T11.Done
MWX | Modbus Network Write
Device | @IntSerModbusClient
Unit ID | 1
Function Code
Modbus Address 4… + offset value entered below
| 6 - Write Single Register
To Modbus Offset Address | 2331
From Do-more Memory Address | Drive_speed_b
On Success, JMP to stage | Close_roof_apr
On Error, Set bit | C208

Dome encoder input to PLC
Dome_encoder_in

Close count mid limit
Close_count_mid
$Dome_encoder.iReg1 D102
SG | Stage
Close_roof_apr
Stage | S6

S6
28

$On
ST1
E/R
TMRDOWN | Down Timer
Dome_tout
Timer Struct | T0
Preset (ms) | Tout_close_apr
COPY | | | Copy Data
# | Source | Destination | Count

1 Dome_tout.Acc | Curr_tout_tmr | 1
2 Dome_tout.Acc Cls_apr_tout_tmr | 1
Page 37 | Drive

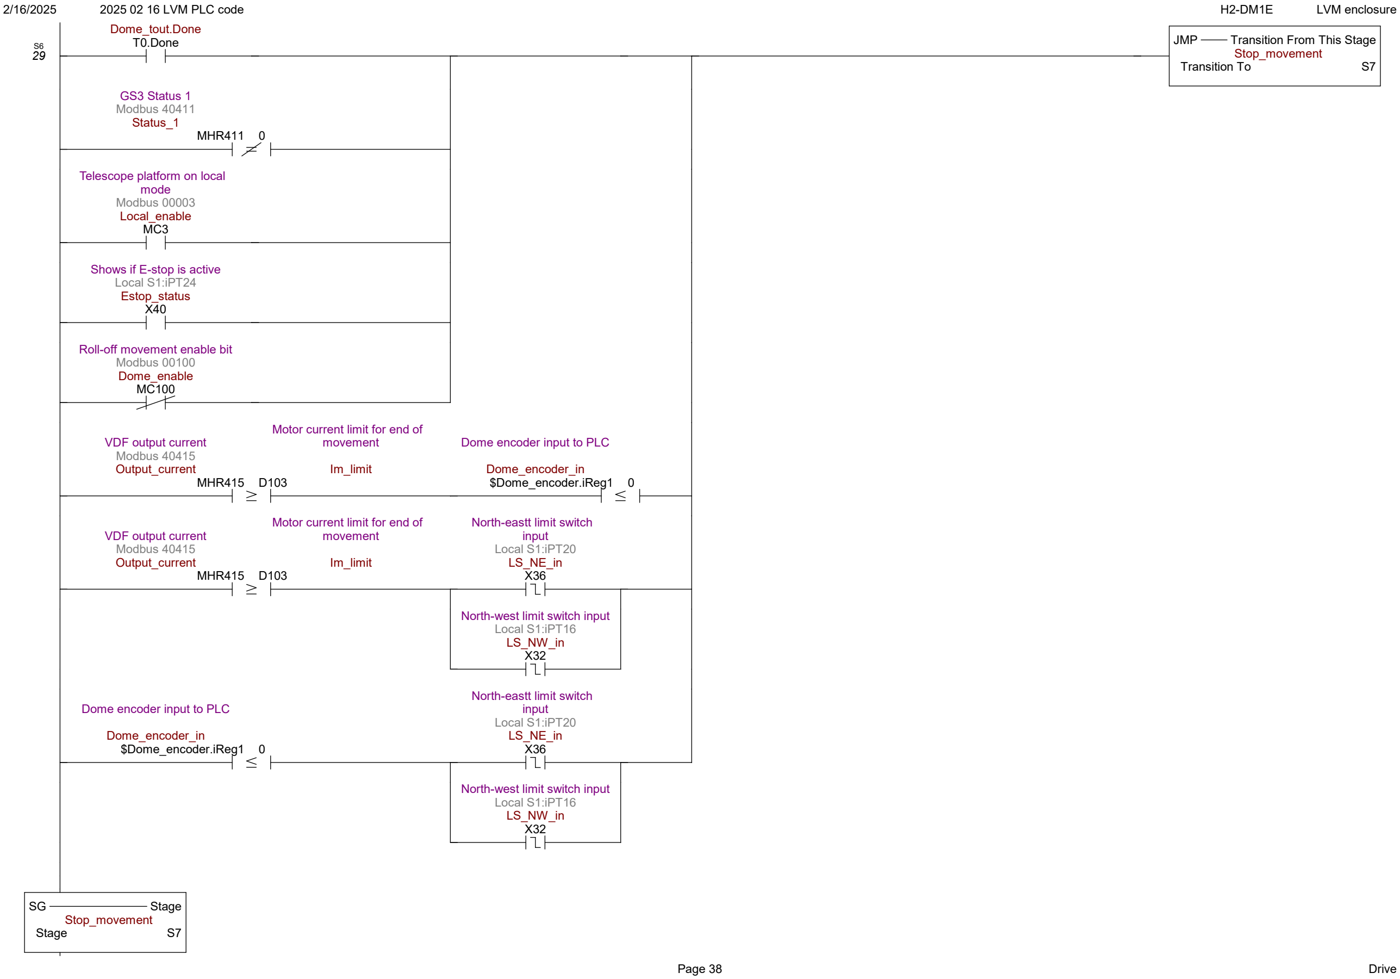
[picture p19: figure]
Dome_tout.Done; T0.Done; JMP; Transition From This Stage; Stop_movement; Transition To; GS3 Status 1 Modbus 40411 Status_1; MHR411 0; Telescope platform on local mode Modbus 00003 Local_enable MC3; Shows if E-stop is active Local S1:iPT24 Estop_status X40; Roll-off movement enable bit Modbus 00100 Dome_enable MC100; VDF output current Modbus 40415 Output_current; Motor current limit for end of movement; Im_limit; MHR415 D103; Dome encoder input to PLC; Dome_encoder_in $Dome_encoder.iReg1 0; North-eastt limit switch input Local S1:iPT20 LS_NE_in X36; North-west limit switch input Local S1:iPT16 LS_NW_in X32; Stage; Page 38; Drive

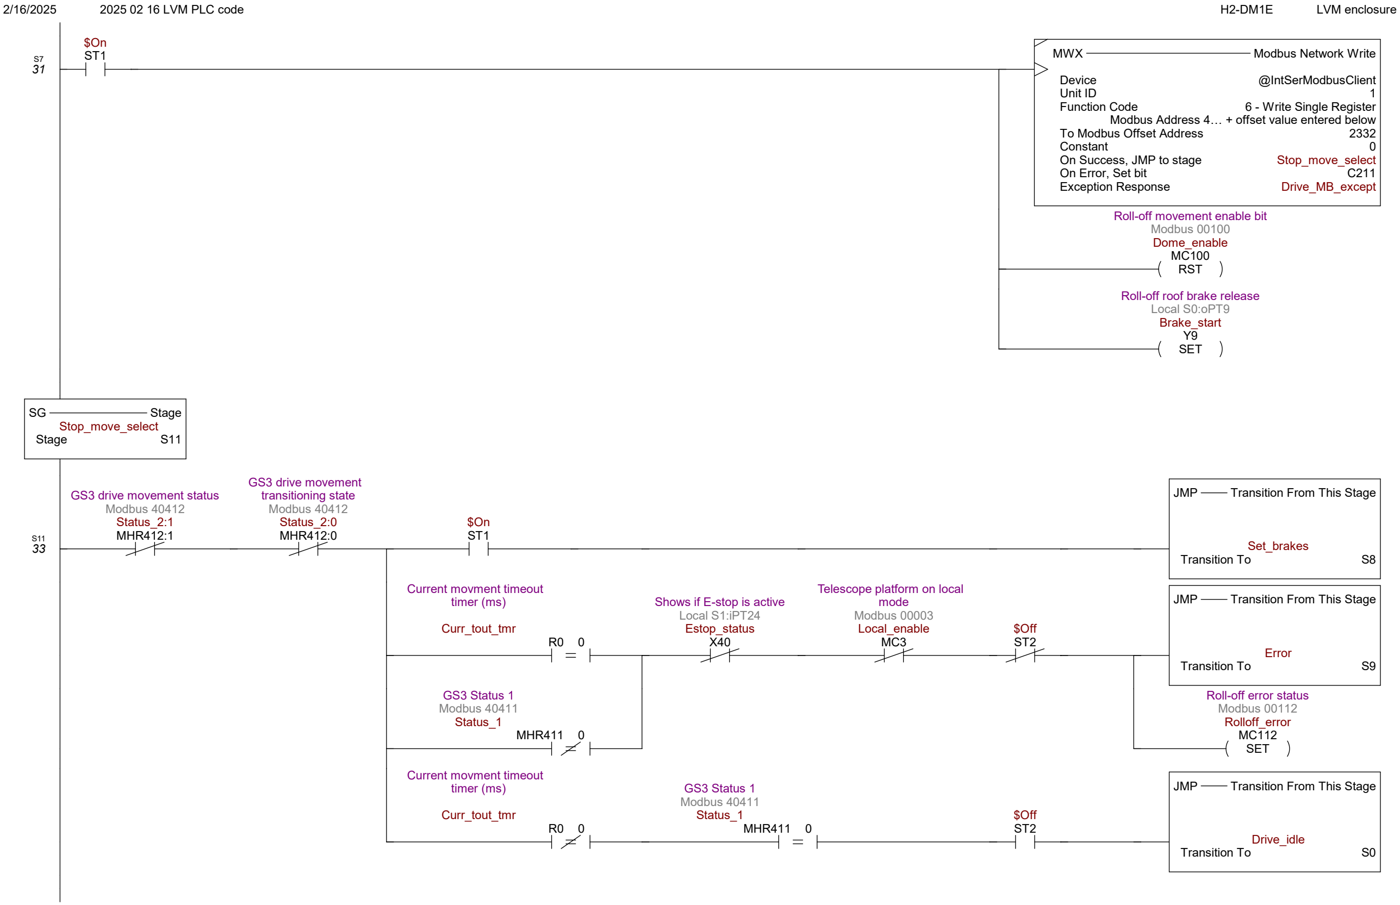
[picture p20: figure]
MWX; Modbus Network Write; Device; @IntSerModbusClient; Unit ID; Function Code; 6 - Write Single Register; To Modbus Offset Address; Constant; On Success, JMP to stage; Stop_move_select; On Error, Set bit; Exception Response; Drive_MB_except; RST; Roll-off movement enable bit Modbus 00100 Dome_enable MC100; SET; Roll-off roof brake release Local S0:oPT9 Brake_start Y9; Stage; GS3 drive movement status Modbus 40412 Status_2:1 MHR412:1; GS3 drive movement transitioning state Modbus 40412 Status_2:0 MHR412:0; JMP; Transition From This Stage; Set_brakes; Transition To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

Modbus Address 4… + offset value entered below

Page 39 | Drive

Page 40 | Drive

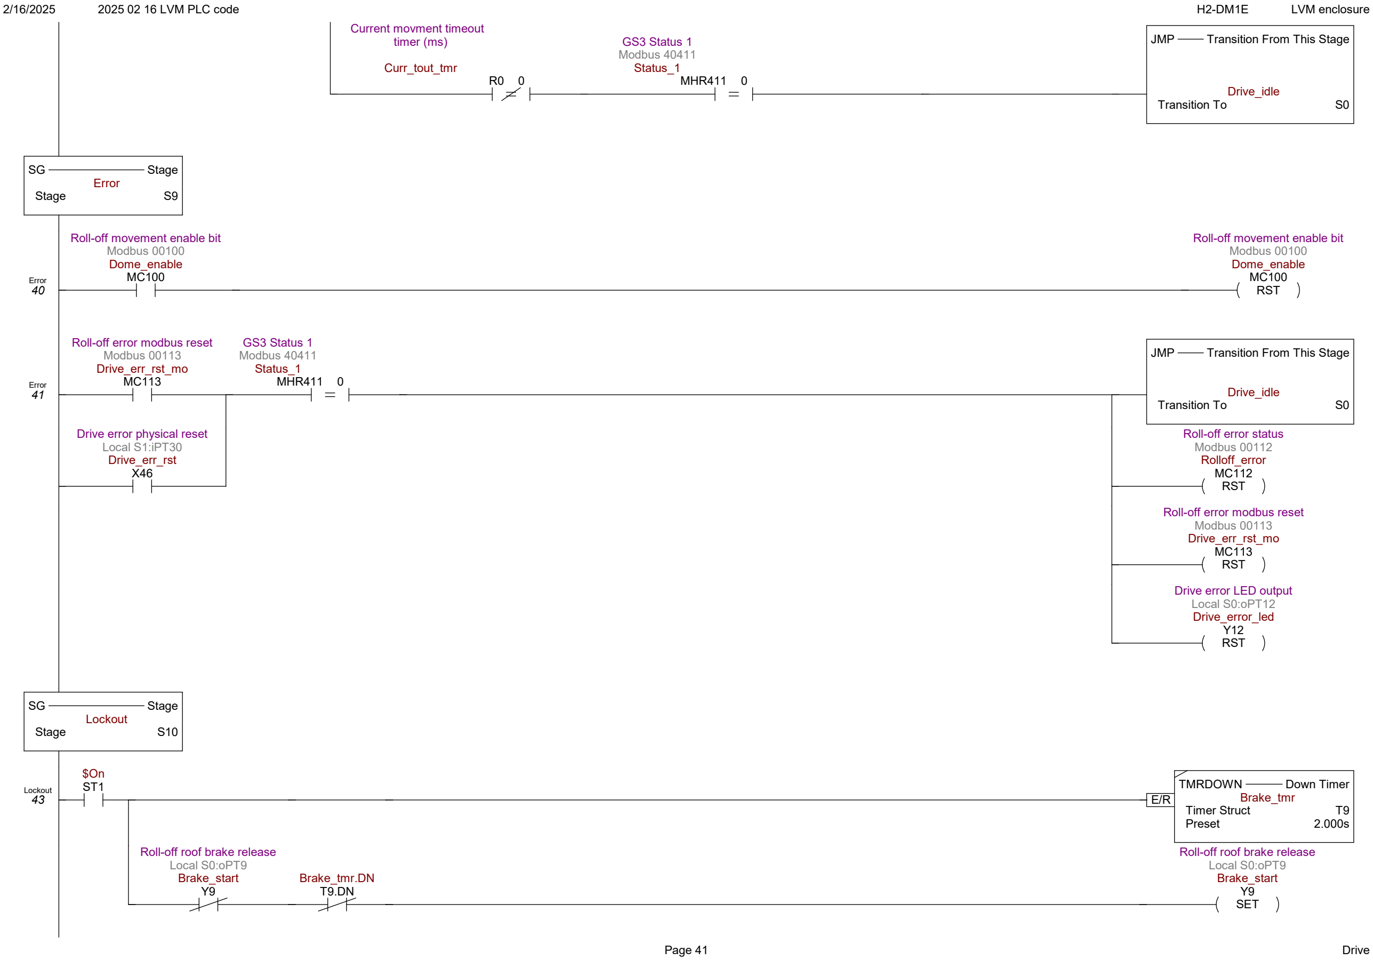
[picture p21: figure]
Current movment timeout timer (ms); Curr_tout_tmr; GS3 Status 1 Modbus 40411 Status_1 MHR411 0; JMP; Transition From This Stage; Drive_idle; Transition To; Stage; Error; Error 40; Roll-off movement enable bit Modbus 00100 Dome_enable MC100; RST; Error 41; Roll-off error modbus reset Modbus 00113 Drive_err_rst_mo MC113; Drive error physical reset Local S1:iPT30 Drive_err_rst X46; Roll-off error status Modbus 00112 Rolloff_error MC112; Drive error LED output Local S0:oPT12 Drive_error_led Y12; Lockout; Lockout 43; TMRDOWN; Down Timer; Brake_tmr; Timer Struct; Preset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

Page 42 | Drive

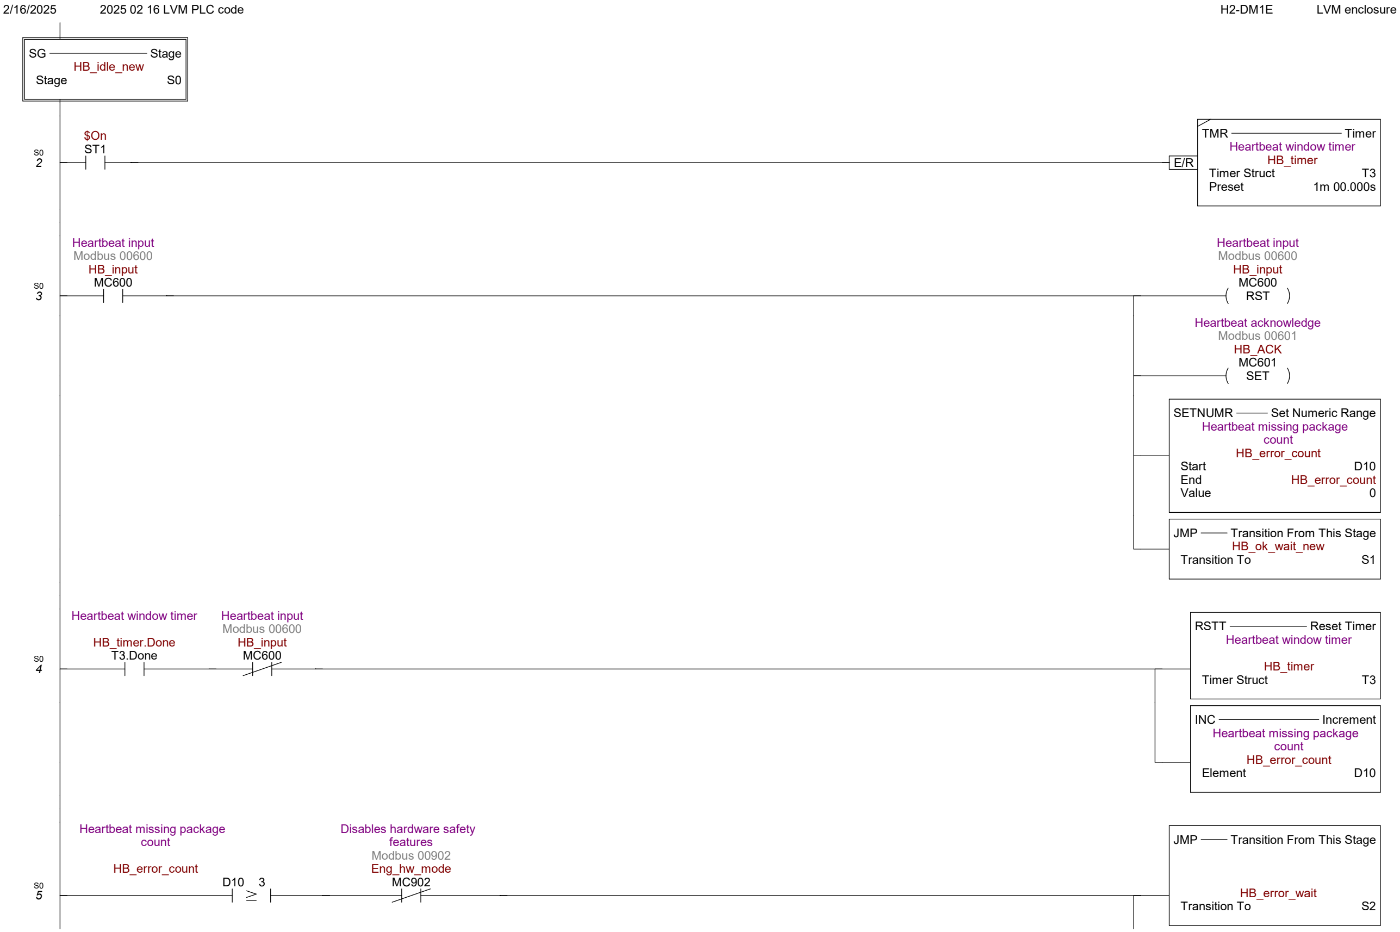
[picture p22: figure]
Stage; HB_idle_new; TMR; Timer; Heartbeat window timer HB_timer; Timer Struct; Preset; Heartbeat input Modbus 00600 HB_input MC600; RST; SET; Heartbeat acknowledge Modbus 00601 HB_ACK MC601; SETNUMR; Set Numeric Range; Heartbeat missing package count HB_error_count; Start; End; HB_error_count; Value; JMP; Transition From This Stage; HB_ok_wait_new; Transition To; Heartbeat window timer; HB_timer.Done T3.Done; RSTT; Reset Timer; HB_timer; INC; Increment; Element; Heartbeat missing package count; Disables hardware safety features Modbus 00902 Eng_hw_mode MC902; HB_error_wait

Page 43 | Heartbeat

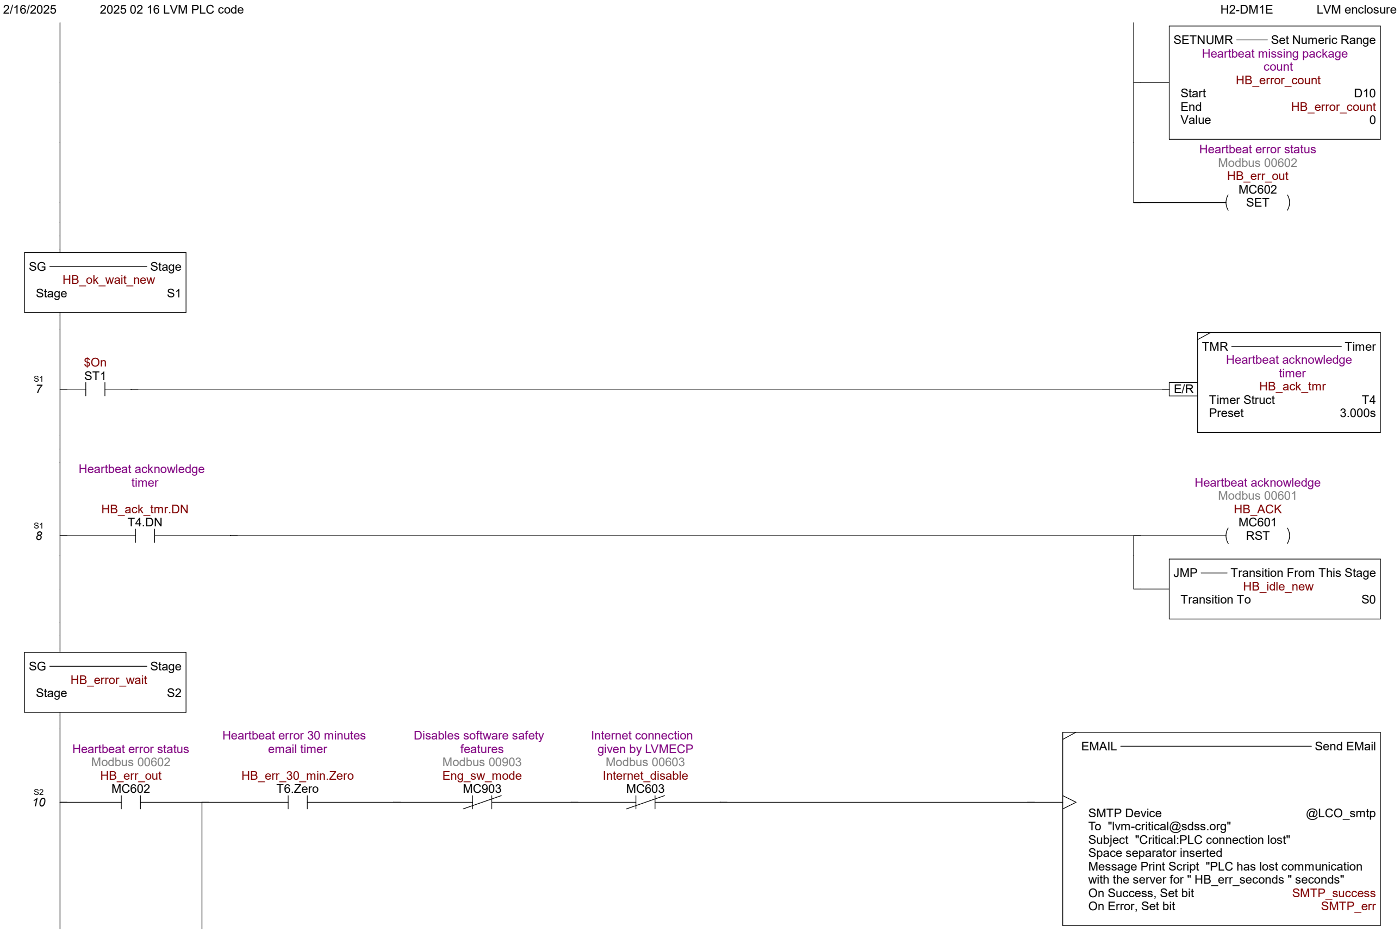
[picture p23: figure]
SETNUMR; Set Numeric Range; Heartbeat missing package count HB_error_count; Start; End; HB_error_count; Value; SET; Heartbeat error status Modbus 00602 HB_err_out MC602; Stage; HB_ok_wait_new; TMR; Timer; Heartbeat acknowledge timer HB_ack_tmr; Timer Struct; Preset; Heartbeat acknowledge timer; HB_ack_tmr.DN T4.DN; RST; Heartbeat acknowledge Modbus 00601 HB_ACK MC601; JMP; Transition From This Stage; HB_idle_new; Transition To; HB_error_wait; Heartbeat error 30 minutes email timer; HB_err_30_min.Zero T6.Zero; Disables software safety features Modbus 00903 Eng_sw_mode MC903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

Message Print Script "PLC has lost communication with the server for " HB_err_seconds " seconds"

Page 44 | Heartbeat

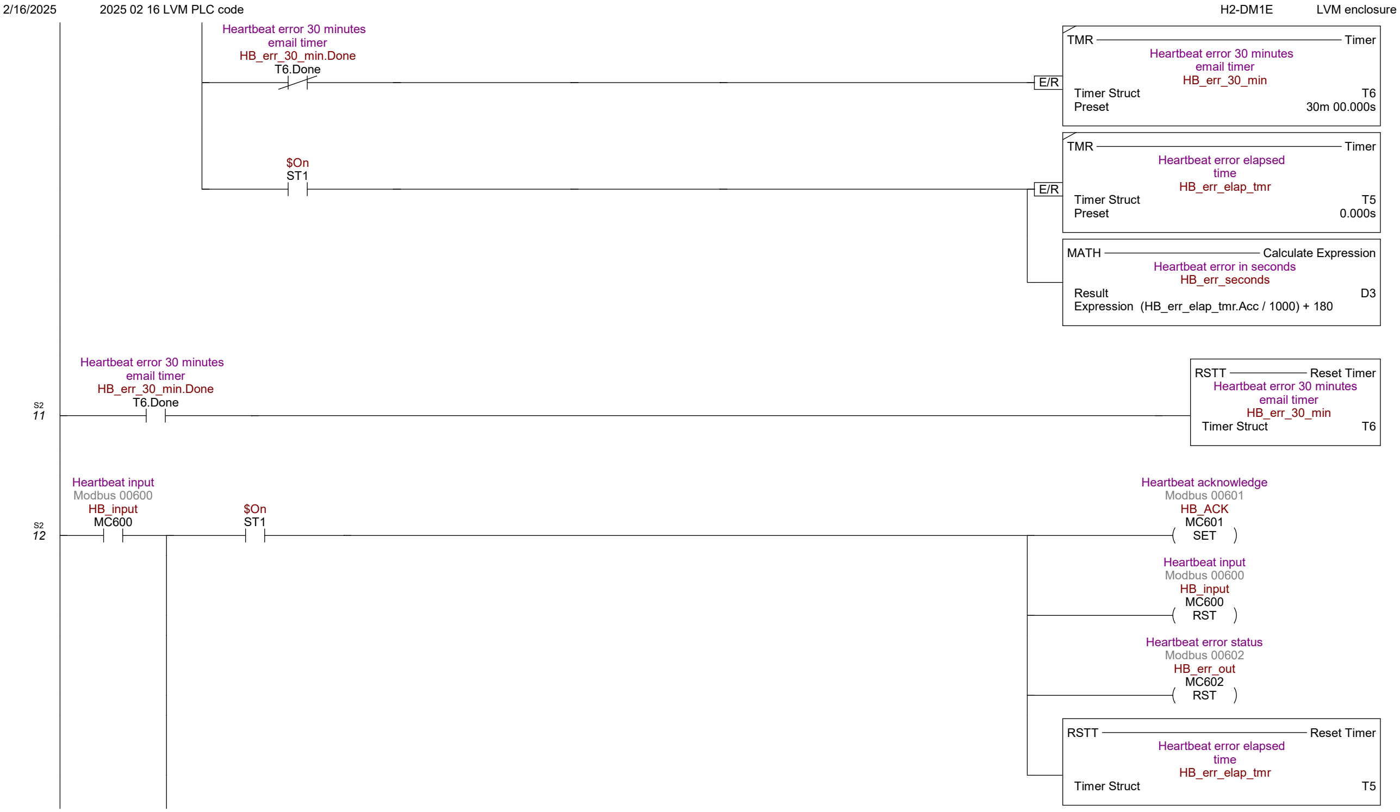
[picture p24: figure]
Heartbeat error 30 minutes email timer HB_err_30_min.Done T6.Done; TMR; Timer; Heartbeat error 30 minutes email timer HB_err_30_min; Timer Struct; Preset; Heartbeat error elapsed time HB_err_elap_tmr; MATH; Calculate Expression; Heartbeat error in seconds HB_err_seconds; Result; RSTT; Reset Timer; Heartbeat input Modbus 00600 HB_input MC600; SET; Heartbeat acknowledge Modbus 00601 HB_ACK MC601; RST; Heartbeat error status Modbus 00602 HB_err_out MC602

Expression (HB_err_elap_tmr.Acc / 1000) + 180

Page 45 | Heartbeat

Disables software safety
features
Modbus 00903
Eng_sw_mode
MC903
EMAIL | Send EMail
SMTP Device | @LCO_smtp
To "lvm-critical@sdss.org"
Subject "Critical: PLC conection restored"
Space separator inserted
Message Print Script "PLC to server communication restored after " HB_err_seconds " seconds"
On Success, JMP to stage | HB_ok_wait_new
On Error, Set bit | SMTP_err

Disables software safety
features
Modbus 00903
Eng_sw_mode
MC903
JMP | Transition From This Stage

HB_ok_wait_new
Transition To | S1

S2

### 13 NOP

Page 46 | Heartbeat

1

$FirstScan
ST0

Internet connection
given by LVMECP
Modbus 00603
Internet_disable
MC603
NETTIME | SNTP Client
Device | @IntEthernet
SNTP Server IP Address | 190.102.231.152
UDP Port Number | 123
Network Timeout (ms) | 1000
On Success, Set bit | NTP_read_ok
On Error, Set bit | NTP_read_err

$Now.Hour
SDT0.Hour 12

$Now.Minute
SDT0.Minute 00

$Now.Second
SDT0.Second 00

### 2 NOP

Page 47 | NTP

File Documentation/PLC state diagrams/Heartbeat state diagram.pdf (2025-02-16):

HB_error_count = 0 HB_ACK = 1 HB_input = 0; HB_input; HB_error_count ≥ 3 && not(eng_hw_mode); HB_ok_wait_new (3 sec); Timeout timer (60 sec); HB_ack_tmr.done Reset HB_timer; HB_error_count +=1; HB_timer.Done && not(HB_input); HB_err_out = 1 HB_error_count = 0; HB_error_w ait (30 m); Send e-mail; HB_err_30_min.Zero && not (Eng_sw_mode || Internet_disable); Reset 30 m timer; HB_input && not(Eng_sw_mode); HB_input && Eng_sw_mode

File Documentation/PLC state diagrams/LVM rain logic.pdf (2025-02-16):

No rain; It's rainning?; Rain rain_mod = 1; yes; Rain stopped?; 15 min countdown; Countdown finished?; rain_mod = 0; Rain sensor has inverted logic:; 1 = no rain. 0 = rain.; Rain out has direct logic. 0 = no rain. 1 = rain.

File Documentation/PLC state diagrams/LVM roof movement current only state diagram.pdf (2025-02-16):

Dome_enable ˄ not(Local_enable ˅ Estop_status) ˄ Status_2:4 ==0; S0 IDLE; remote_dir = 0; drive_dir ≠ 0; S5 Lockout; Rolloff_lout = 1; Local_enable; S2 Start movement 100ms_delay_tmr Brake_tmr (2 s) Brake_start = 1; S3 Movement Tout = 165 s; Status_2:0 ˄ Status_2:1 ˄; not(Brake_start ˅ Local_enable ˅ Estop_status); S4 Error drive_enable = 0 error = 1 error_led = 1; (Drive_error_rst_mod ˅ Drive_err_rst) ˄ Status_1 == 0; GS3_run = 1; Dome_enable ˄ VDF_des_freq == 70 ˄ not(Local_enable ˅ Estop_status) ˄ Brake_tmr.done ˄ Brake_start; Rolloff_error = 0 Drive_err_rst_mo = 0 Drive_error_led = 0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

not(Status_2:3 ˅ Status_2:4 ˅ Dome_closed) ˄

(Output_current ≥ 120 ˅ not(Dome_enable) ˅ Local_enable) ˄ not(Dome_Tout.Done ˅ Status_1 ≠ 0 ˅ Estop_status)

Dome_Tout.Done ˅ Status_1 ≠ 0 ˅ Estop_status

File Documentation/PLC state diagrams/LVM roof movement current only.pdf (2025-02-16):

IDLE; Local_enable == 1; Local_enable == 0; lockout wait Rolloff_lout = 1; drive_dir ≠ 0; drive_dir = 0; Dome_enable ˄ not(Local_enable ˅ Estop_status) ˄ Status_2:4; yes; START MOVEMENT drive_enable = 1; drive_enabled?; Roof closing start coundown; Output current > 120 and no error; Activate brake; Brakes disengaged; Start 2 second timer; Has the dome stopped and have the two secomds passed; Brake_start = 0; VDF error, timeout done, Estop; Idle; Error wait Rolloff_error = 1 Error_led = 1; not(VDF error) ˄ not(E-stop); Start 2; second timer

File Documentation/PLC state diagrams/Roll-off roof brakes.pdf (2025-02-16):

GND; 1 A slow fuse; Relay (781-1C-24D); VFD relay (GS3-23P0) P3.11 = 00; Motor brake

PLC digital output (Y9/B1) 24 V power suppy

# Roll-off brake diagram

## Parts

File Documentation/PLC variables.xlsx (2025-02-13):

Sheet: Variables
DeviMCe | Element | FunMCtion | Meaningful values / Range | Other Information | DesMCription
Interlock | MC1 | Key |  |  | show key position
 | MC2 | Door status |  |  | Door open/close
 | MC2 | Door power |  |  | Magnet lock powered on/off
 | MC3 | drive interlock state |  |  | Show actual
 | MC4 | E- relay status |  |  | Show e-relay status
 | MC5 | E-stop modbus
Lights | MC235 | Control room lights new status |  | Changes relay
 | MC236 | Utilities room lights new status |  | Changes relay
 | MC237 | Spectrograph room lights new status |  | Changes relay
 | MC238 | UMA lights new status |  | Changes relay
 | MC239 | Tel Plat bright lights new status |  | Changes relay
 | MC240 | Tel plat red new status |  | Changes relay
 | MC335 | Control room lights status
 | MC336 | Utilities room lights status
 | MC337 | Spectrograph room lights status
 | MC338 | UMA lights status
 | MC339 | Tel Plat bright lights status
 | MC340 | Tel plat red status
Shutter movement | MC100 | Drive enable
 | MC101 | Drive state
 | MC102 | Motor direction
 | MC103 | Drive brake
 | D104-105 | Drive velocity
 | MC105 | NE limit switch status
 | MC106 | NW limit switch status
 | MC107 | SE limit switch status
 | MC108 | SW limit switch status
 | MC110 | OverCurrent
 | D120 | Open timeout
 | D121 | Close timeout
 | MC122 | Open small move timeout
 | D130 | Drive Current
 | T0 | Timout_error
 | D150 | dome Counter
EmergenMCy stop | MC200 | E-Stop
 | MC201 | E-Stop status
 | MC202 | E-relay reset.

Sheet: Input
Device | Element | Function | Meaningful values / Range | Other Information | Description
 | X16 | Door locked |  | Open/Close
 | X17 | Door unlocked
 | X18 | Door closed
 | X40 | E-Stop
 |  |  |  |  | Shows actual driving state
Lights | X10 | Control room lights curr det
 | X11 | Utilities room lights curr det
 | X12 | Spectrograph room lights curr det
 | X13 | UMA lights curr det
 | X29 | Tel Plat bright lights curr det
 | X30 | Tel plat red curr det
Shutter movement | X39 | NE limit switch
 | X32 | NW limit switch
 | X38 | SE limit switch
 | X34 | SW limit switch
 | WX0 | Motor counter
Rain sensor | X47 | Rain sensor NC output

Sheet: Output
Device | Element | Function | Meaningful values / Range | Other Information | Description
E-stop | Y6 | PLC E-stop
 | Y7 | release PLC E-stop
Lights | Y0 | Control room lights relay
 | Y1 | Utilities room lights relay
 | Y2 | Spectrograph room lights relay
 | Y3 | UMA lights relay
 | Y4 | Tel Plat bright lights relay
 | Y5 | Tel plat red relay
Shutter movement | Y9 | Brake
HVAC | Y8 | HVAC flag |  |  | Flag to start telescope fans

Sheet: Modbus
Device | Element | Function | Read/Write | Meaningful values / Range | Other Information | Description
Interlock | MC1 | Door locked | R | X0
 | MC2 | Door closed | R
 | MC3 | Local enable | R
Lights | MC235 | Control room lights toggle | W |  | Changes relay
 | MC236 | Utilities room lights toggle | W |  | Changes relay
 | MC237 | Spectrograph room lights toggle | W |  | Changes relay
 | MC238 | UMA lights toggle | W |  | Changes relay
 | MC239 | Tel Plat bright lights toggle | W |  | Changes relay
 | MC240 | Tel plat red light toggle | W |  | Changes relay
 | MC335 | Control room lights status | R
 | MC336 | Utilities room lights status | R
 | MC337 | Spectrograph room lights status | R
 | MC338 | UMA lights status | R
 | MC339 | Tel Plat bright lights status | R
 | MC340 | Tel plat red light status | R
Roll-off movement | MC99 | Dome mode selector | W |  |  | Selects between normal operation and overcurrent only mode.
 | MC100 | Drive enable | W
 | MC101 | Motor direction | W | 0 closes / 1 opens.
 | MC102 | Drive state | R
 | MC105 | NE limit switch status | R
 | MC106 | NW limit switch status | R
 | MC107 | SE limit switch status | R
 | MC108 | SW limit switch status | R
 | MC109 | Dome closed | R
 | MC110 | Dome open | R
 | MC111 | Rolloff_lout | R
 | MC112 | Rolloff_error | R
 | MC113 | Drive_err_rst_mo | W
 | MHR130 | Drive current copy (MHR415) | R
 | MHR150 | Dome Counter | R
 | MHR151 | Dome pos in mm (theoretical) | R
 | MHR150 | Dome pos in mm (scale function) | R
 | MHR152 | Dome speed | R
 | MHR400 | Present Fault Record | R | Not implemented
 | MHR401 | Second Most Recent Fault Record | R | Not implemented
 | MHR402 | Third Most Recent Fault Record | R | Not implemented
 | MHR403 | Fourth Most Recent Fault Record | R | Not implemented
 | MHR404 | Fifth Most Recent Fault Record | R | Not implemented
 | MHR405 | Sixth Most Recent Fault Record | R | Not implemented
 | MHR411 | Status Monitor 1 | R
 | MHR412 | Status monitor 2 | R
 | MHR413 | Commanded frequency | R
 | MHR414 | Output Frequency | R
 | MHR415 | Output Current | R
 | MHR417 | Output Voltage | R
 | MHR418 | Motor current RPM | R
 | MHR510 | User defined drive frequency | W | Deprecated
Emergency stop | MC200 | E-Stop status | R
 | MC201 | E-Stop | W
 | MC202 | E-relay reset | W
Hearthbeat | MC600 | Heartbeat input | W
 | MC601 | Heartbeat aknowledge | R
 | MC602 | Heartbeat error | R
 | MC603 | Internet not available | W
ODH Sensor | MHR600 | O2 precentage utilities room | R
 | MHR601 | O2 percentage spectrograph room | R
 | MHR602 | ODH error code utilities room | R
 | MHR603 | ODH error code spectrograph room | R
 | MHR604 | ODH status byte utilities room | R
 | MHR605 | ODH status byte spectrograph room | R
Environmental | MC700 | Rain sensor output | R
 | MHR700 | Rain conunter (will count every time the rain sensor transitions from 1 to 0 | R
 | MHR701 | No rain countdown | R
Engineering mode | MC900 | Engineering hardware mode | W
 | MC901 | Engineering software mode | W
 | MC902 | Enineering hardware status | R
 | MC903 | Engineering software status | R

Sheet: GS3 read
GS3 code | GS3 Var name | Modbus GS3 Var | Do more Var
P6.31 | Present Fault Record | 41568 | MHR400
P6.32 | Second Most Recent Fault Record | 41569 | MHR401
P6.33 | Third Most Recent Fault Record | 41570 | MHR402
P6.34 | Fourth Most Recent Fault Record | 41571 | MHR403
P6.35 | Fifth Most Recent Fault Record | 41572 | MHR404
P6.36 | Sixth Most Recent Fault Record | 41573 | MHR405
P9.26 | Serial Comm (RS-485) Speed Reference | 42331 | MHR410
 | Status monitor 1 | 48449 | MHR411
 | Status monitor 2 | 48450 | MHR412
 | Frequency Command F | 48451 | MHR413
 | Output Frequency | 48452 | MHR414
 | Output Current A | 48453 | MHR415
 |  |  |  | git

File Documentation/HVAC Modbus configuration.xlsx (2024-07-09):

ID | Name | Function code | Modbus direction | Variable type | Endian | Default value
Device2.AI:1 | Water flow input circuit | 4X (Holding Register) | 1 | float | float | 9999
Device2.AI:2 | Flowmeter AHU Spectrograph | 4X (Holding Register) | 3 | float | Little-endian byte swap | 9999
Device2.AI:3 | Exterior humidity | 4X (Holding Register) | 5 | float | Little-endian byte swap | 9999
Device2.AI:4 | Humidity utilities room | 4X (Holding Register) | 7 | float | Little-endian byte swap | 9999
Device2.AI:5 | Humidity Spectrograph room | 4X (Holding Register) | 9 | float | Little-endian byte swap | 9999
Device2.AI:6 | Humidity telescope platform | 4X (Holding Register) | 11 | float | Little-endian byte swap | 9999
Device2.AI:7 | Water pressure inlet circuit 1 | 4X (Holding Register) | 13 | float | Little-endian byte swap | 9999
Device2.AI:8 | Water pressure inlet circuit 2 | 4X (Holding Register) | 15 | float | Little-endian byte swap | 9999
Device2.AI:9 | Exterior temperature | 4X (Holding Register) | 17 | float | Little-endian byte swap | 9999
Device2.AI:10 | Utilities room temperature | 4X (Holding Register) | 19 | float | Little-endian byte swap | 9999
Device2.AI:11 | Spectrograph room temperature | 4X (Holding Register) | 21 | float | Little-endian byte swap | 9999
Device2.AI:12 | Telescope platform temperature | 4X (Holding Register) | 23 | float | Little-endian byte swap | 9999
Device2.AI:13 | Chiller in water temperature | 4X (Holding Register) | 25 | float | Little-endian byte swap | 9999
Device2.AI:14 | AHU in water temperature | 4X (Holding Register) | 27 | float | Little-endian byte swap | 9999
Device2.AI:15 | AHU injection temperature | 4X (Holding Register) | 29 | float | Little-endian byte swap | 9999
Device2.AI:16 | AHU return temperature | 4X (Holding Register) | 31 | float | Little-endian byte swap | 9999
Device2.AI:17 | Chiller out temperature | 4X (Holding Register) | 33 | float | Little-endian byte swap | 9999
Device2.AI:18 | AHU out temperature | 4X (Holding Register) | 35 | float | Little-endian byte swap | 9999
Device2.AO:1 | AHU cold valve (three way valve) | 4X (Holding Register) | 37 | float | Little-endian byte swap | 9999
Device2.BI:1 | System status (on / off) | 0X (Coil Status) | 1 | bool | Null | 9999
Device2.BI:2 | AHU filter status | 0X (Coil Status) | 2 | bool | Null | 9999
Device2.BI:3 | VIN 1 air pressure | 0X (Coil Status) | 3 | bool | Null | 9999
Device2.BI:4 | VIN 2 air pressure | 0X (Coil Status) | 4 | bool | Null | 9999
Device2.BI:5 | Roll-off roof position | 0X (Coil Status) | 5 | bool | Null | 9999
Device2.BO:1 | Status damper 1 (open / close) | 0X (Coil Status) | 6 | bool | Null | 9999
Device2.BO:2 | Status damper 2 (open / close) | 0X (Coil Status) | 7 | bool | Null | 9999
Device2.BO:3 | AHU heater 1 | 0X (Coil Status) | 8 | bool | Null | 9999
Device2.BO:4 | Start/stop Chiller | 0X (Coil Status) | 9 | bool | Null | 9999
Device2.BO:5 | Start/stop Vin 1 | 0X (Coil Status) | 10 | bool | Null | 9999
Device2.BO:6 | Start/stop Vin 2 | 0X (Coil Status) | 11 | bool | Null | 9999
Device2.BO:7 | Start/stop water pump | 0X (Coil Status) | 12 | bool | Null | 9999
Device2.BO:8 | Start/stop AHU | 0X (Coil Status) | 13 | bool | Null | 9999

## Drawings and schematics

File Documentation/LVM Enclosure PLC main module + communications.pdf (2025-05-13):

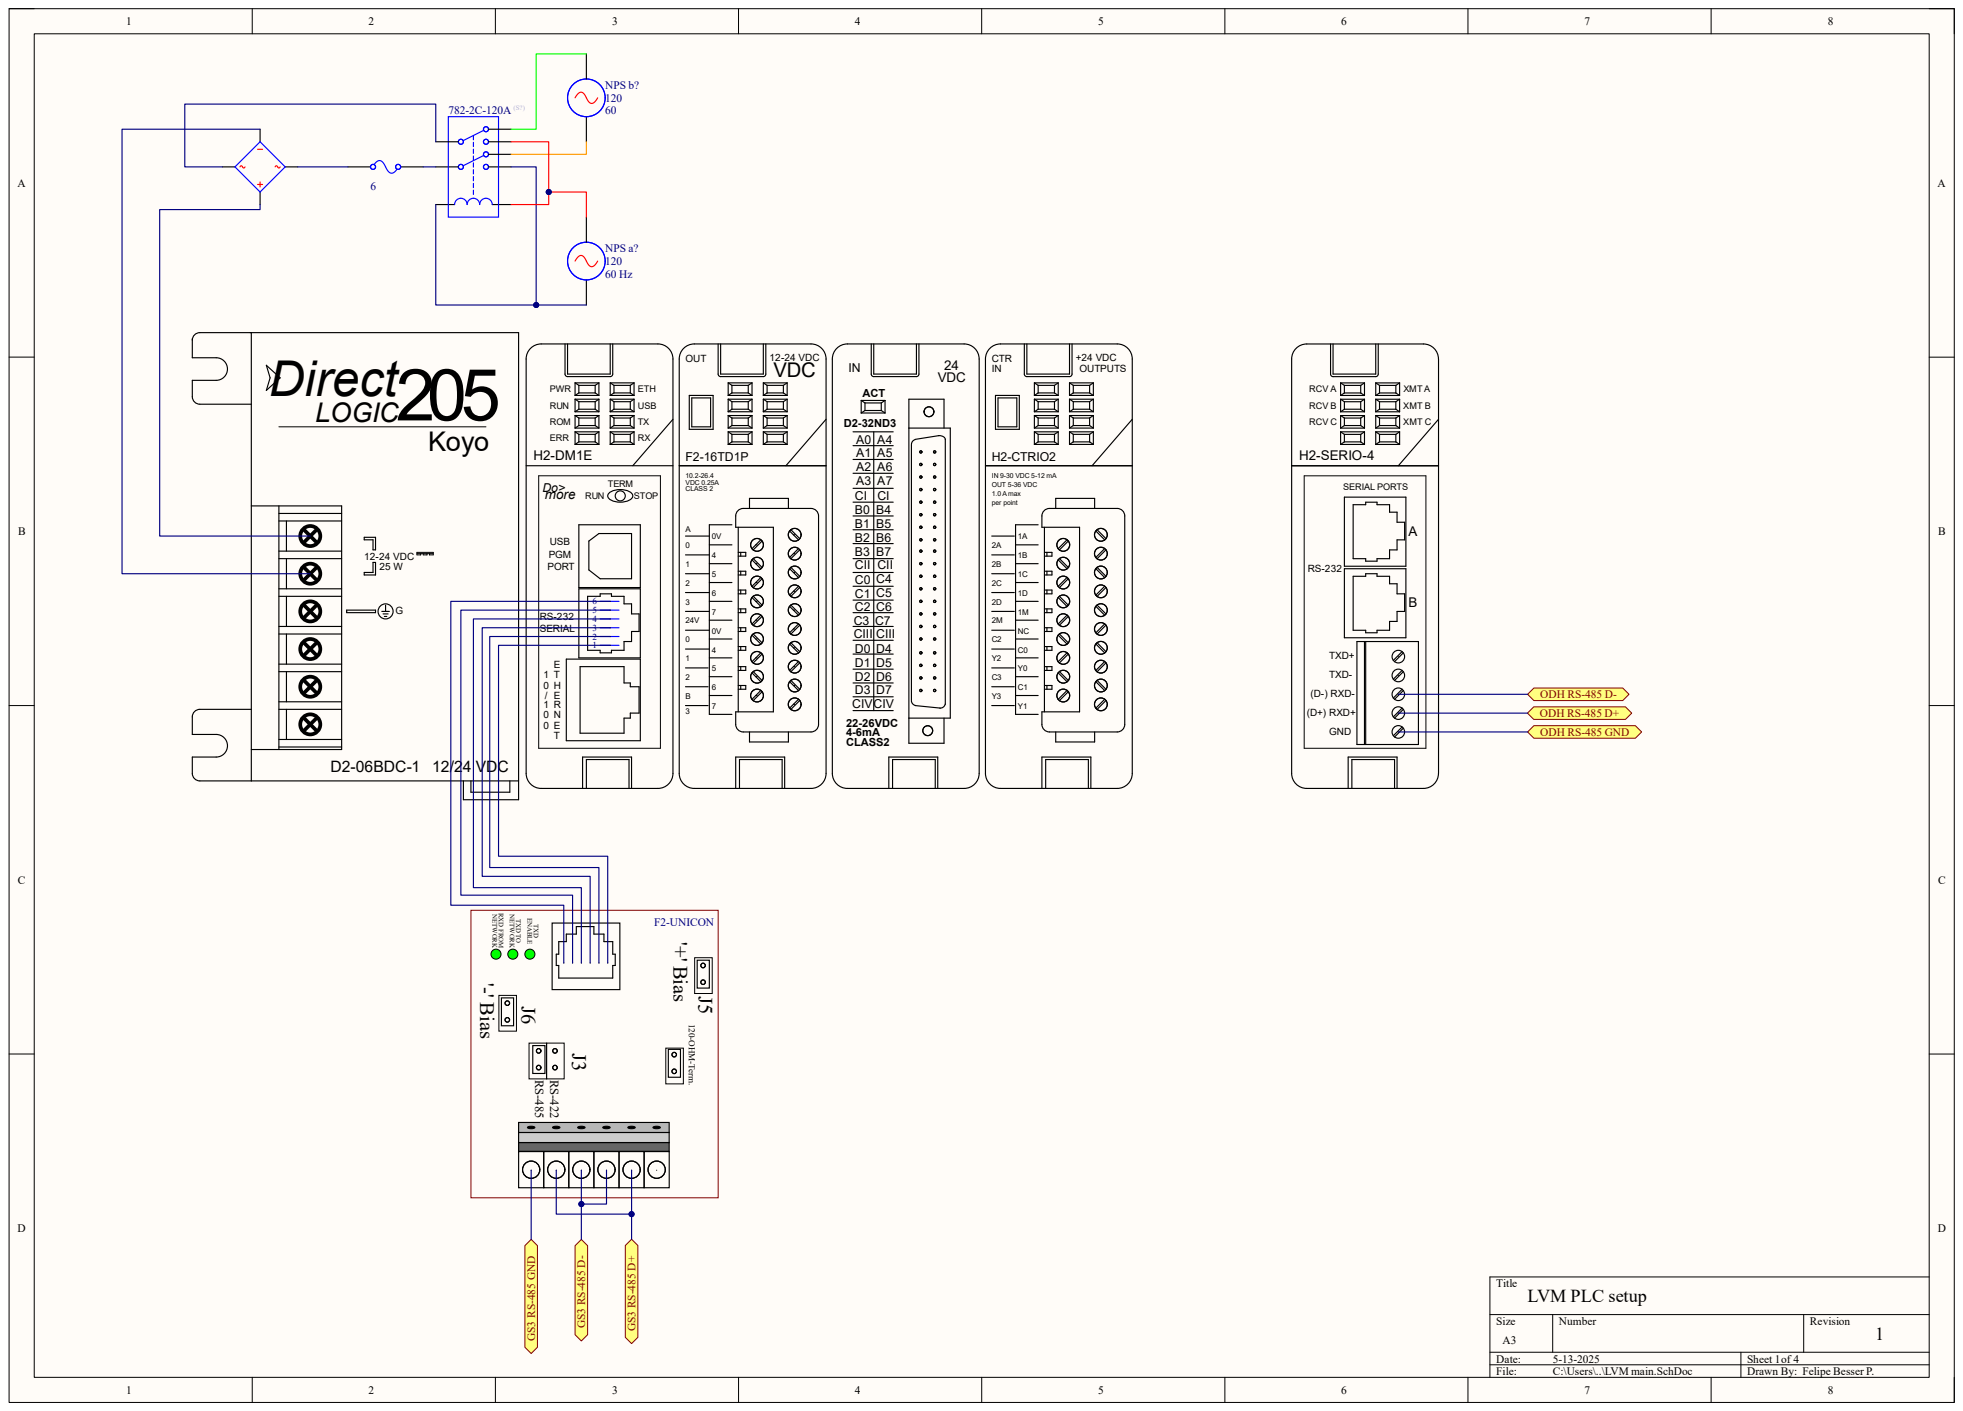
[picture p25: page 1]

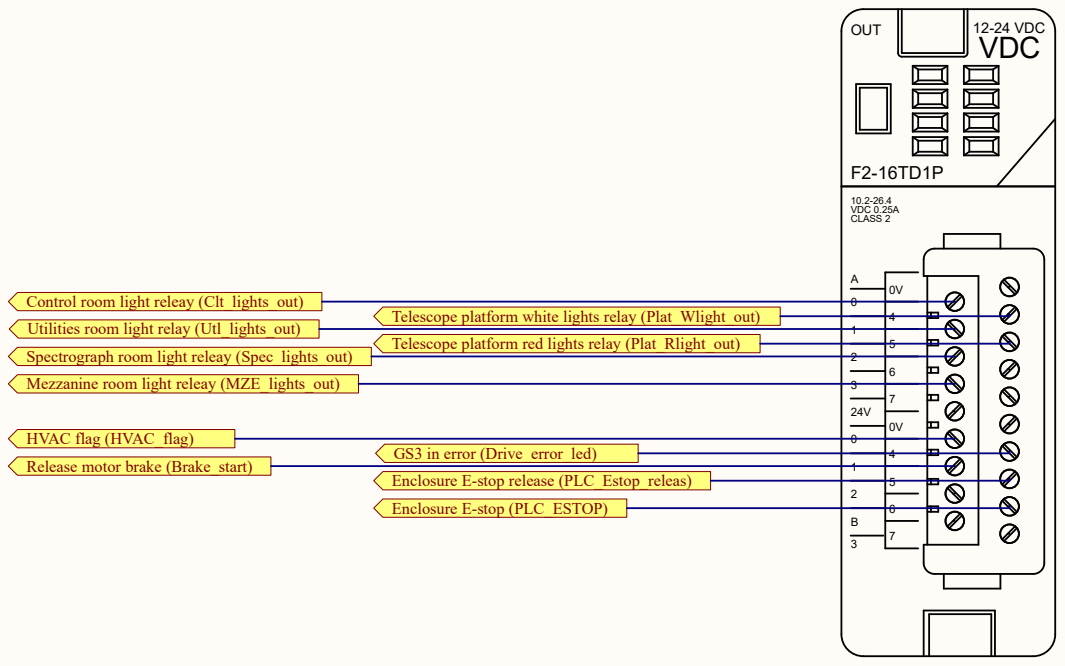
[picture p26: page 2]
Size; Number; Revision; File:; C:\Users\..\PLC out.SchDoc; Drawn By:; OUT; 12-24 VDC; VDC 0.25A; VDC; CLASS 2

Control room light releay (Clt_lights_out)
Utilities room light relay (Utl_lights_out)
Spectrograph room light releay (Spec_lights_out)
Mezzanine room light releay (MZE_lights_out)

Telescope platform white lights relay (Plat_Wlight_out)
Telescope platform red lights relay (Plat_Rlight_out)

HVAC flag (HVAC_flag)
Release motor brake (Brake_start)

GS3 in error (Drive_error_led)
Enclosure E-stop release (PLC_Estop_releas)
Enclosure E-stop (PLC_ESTOP)

Title
Enclosure PLC outputs

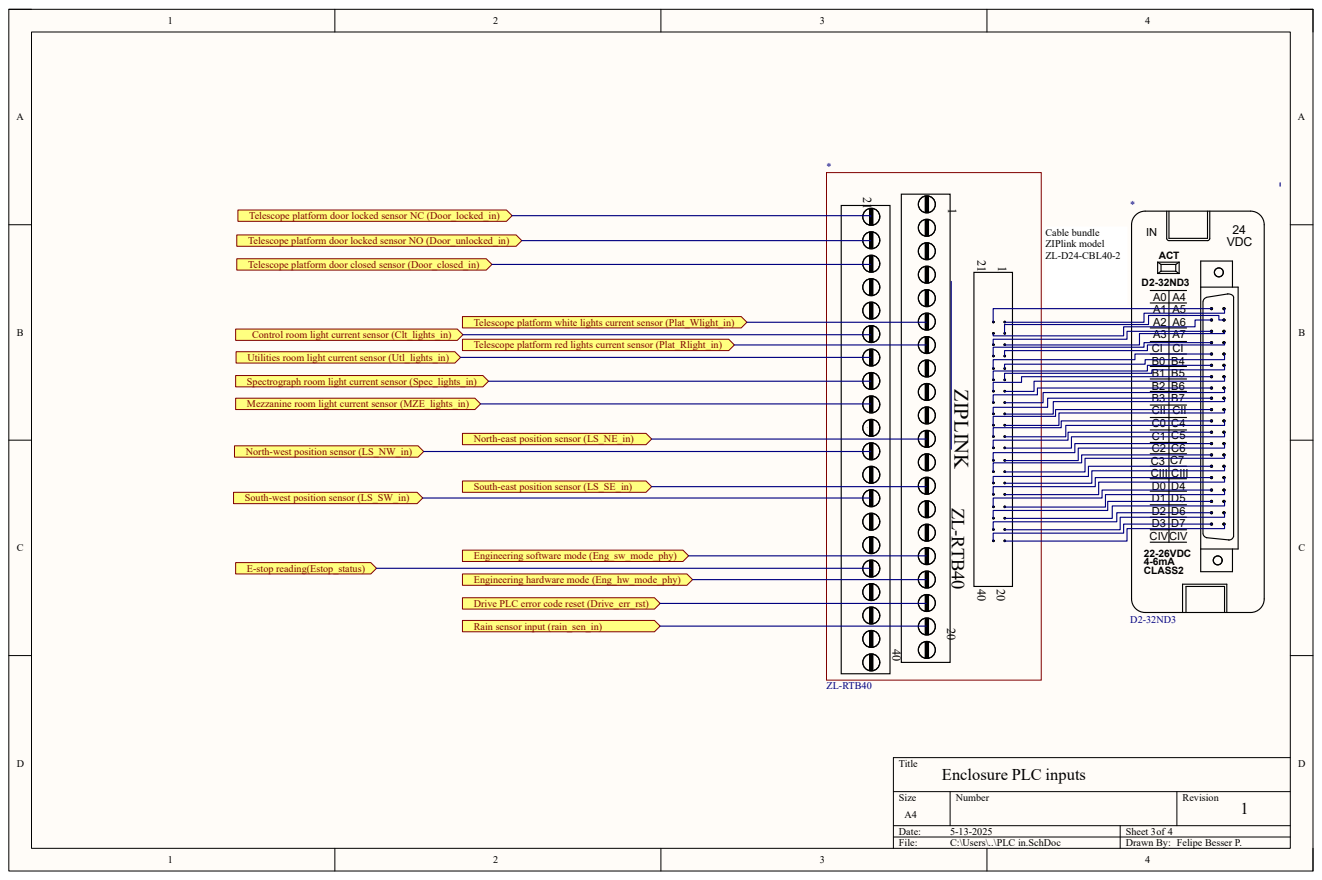
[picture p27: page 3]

Telescope platform door locked sensor NC (Door_locked_in)

Telescope platform door locked sensor NO (Door_unlocked_in)

Telescope platform door closed sensor (Door_closed_in)

Telescope platform white lights current sensor (Plat_Wlight_in)

Control room light current sensor (Clt_lights_in)

Telescope platform red lights current sensor (Plat_Rlight_in)

Utilities room light current sensor (Utl_lights_in)

Spectrograph room light current sensor (Spec_lights_in)

Mezzanine room light current sensor (MZE_lights_in)

North-east position sensor (LS_NE_in)

North-west position sensor (LS_NW_in)

South-east position sensor (LS_SE_in)

South-west position sensor (LS_SW_in)

Drive PLC error code reset (Drive_err_rst)

5

6

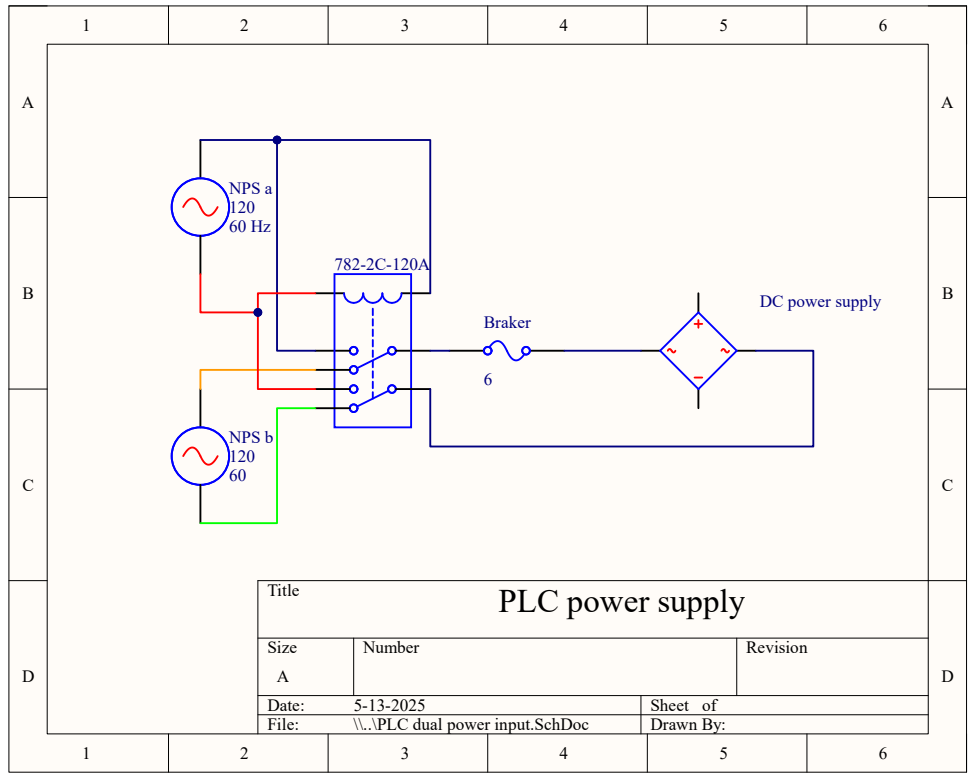
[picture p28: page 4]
Title; Size; Number; Revision; Date:; Sheet of; File:; \\..\PLC dual power input.SchDoc; Drawn By:; NPS a; NPS b; Braker

DC power supply

PLC power supply

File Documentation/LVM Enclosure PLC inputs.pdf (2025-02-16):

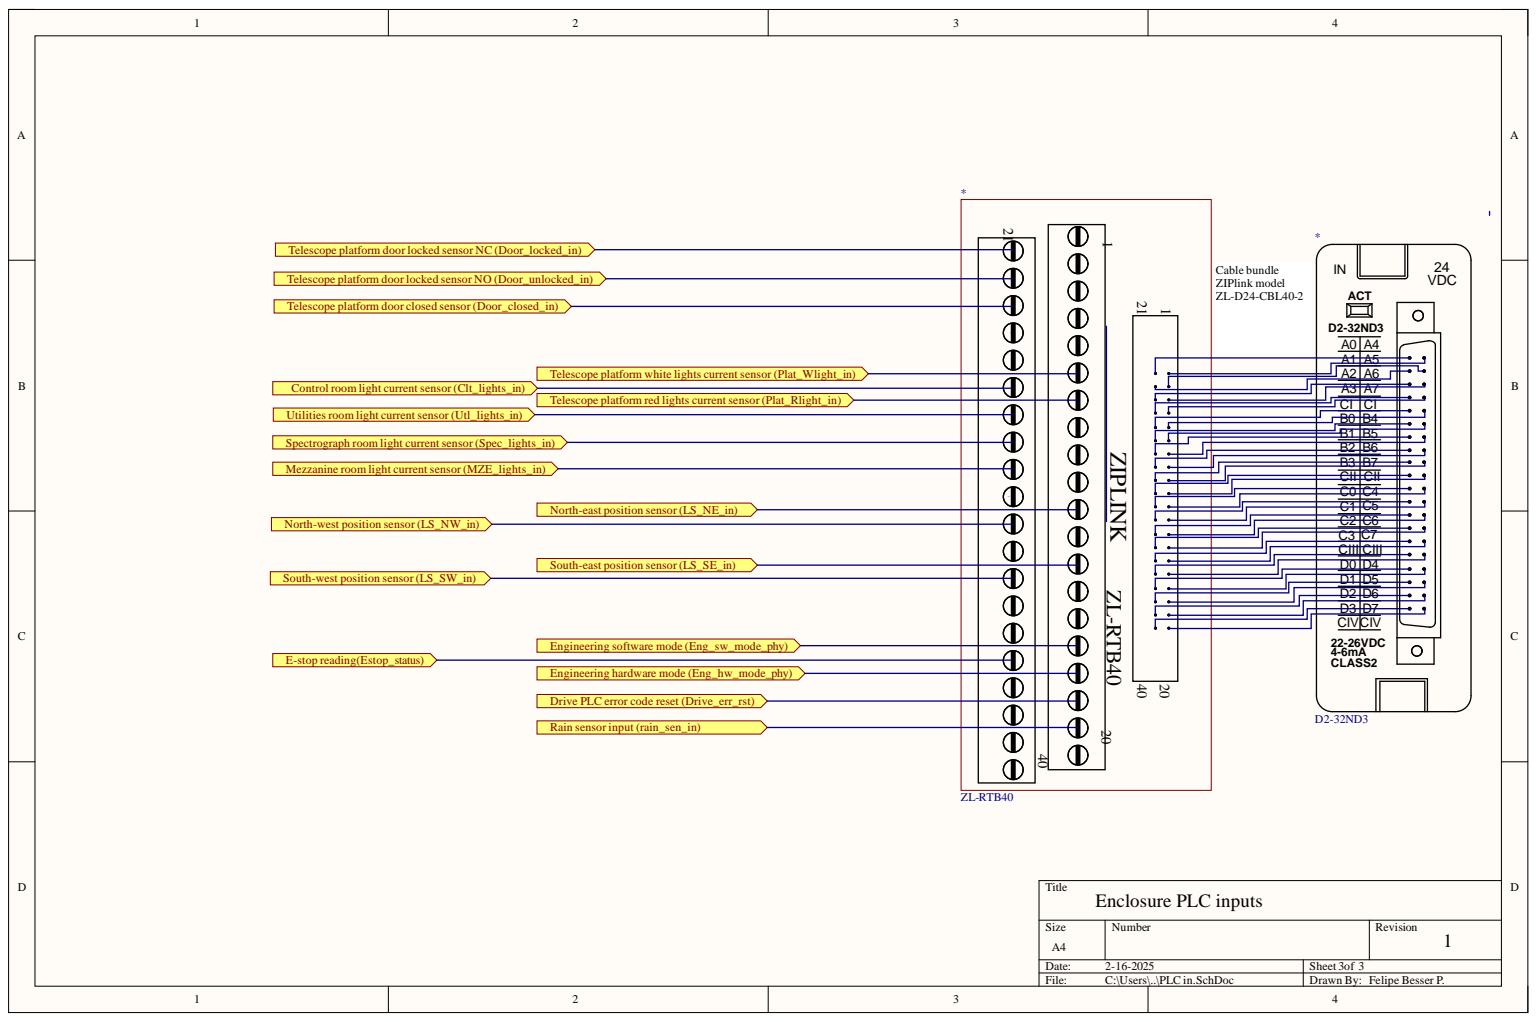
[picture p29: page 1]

Telescope platform door locked sensor NC (Door_locked_in)

Telescope platform door locked sensor NO (Door_unlocked_in)

Telescope platform door closed sensor (Door_closed_in)

Control room light current sensor (Clt_lights_in)

Telescope platform white lights current sensor (Plat_Wlight_in)

A3 | A7
CI | CI

Telescope platform red lights current sensor (Plat_Rlight_in)

Utilities room light current sensor (Utl_lights_in)

Spectrograph room light current sensor (Spec_lights_in)

B2 | B6
B3 | B7
CII | CII
C0 | C4
C1 | C5
C2 | C6
C3 | C7
CIII
D0 | D4
D1 | D5
D2 | D6
D3 | D7
CIVCIV

Mezzanine room light current sensor (MZE_lights_in)

North-east position sensor (LS_NE_in)

North-west position sensor (LS_NW_in)

South-west position sensor (LS_SW_in)

South-east position sensor (LS_SE_in)

Drive PLC error code reset (Drive_err_rst)

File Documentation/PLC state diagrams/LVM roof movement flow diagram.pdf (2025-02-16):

## lockout = (rain ˅ heartbeat_error ˄ dome_open) ˅ e-stop ˅

## local_mode

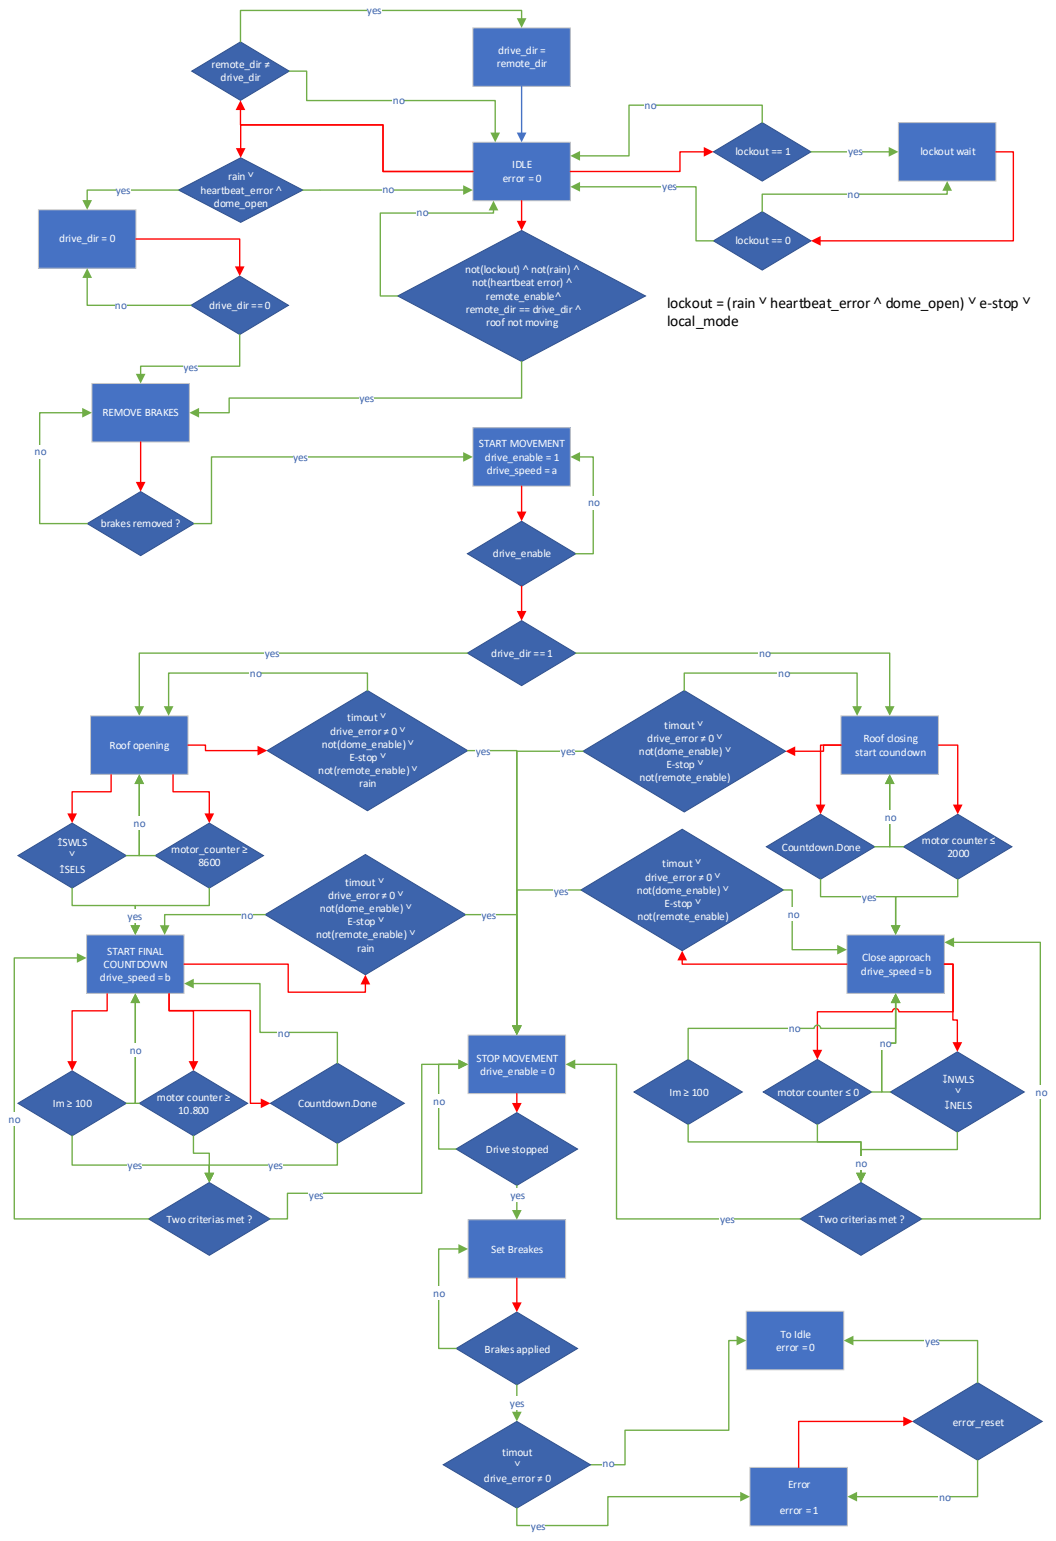
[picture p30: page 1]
IDLE error = 0; lockout == 1; lockout == 0; lockout wait; rain ˅ heartbeat_error ˄ dome_open; remote_dir ≠ drive_dir; drive_dir = remote_dir; drive_dir = 0; drive_dir == 0; REMOVE BRAKES; brakes removed ?; yes; START MOVEMENT drive_enable = 1 drive_speed = a; drive_enable; drive_dir == 1; Roof opening; Roof closing; start coundown; Error; error = 1; timout ˅ drive_error ≠ 0 ˅ not(dome_enable) ˅ E-stop ˅ not(remote_enable) ˅ rain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

not(lockout) ˄ not(rain) ˄
not(heartbeat error) ˄
remote_enable˄
remote_dir == drive_dir ˄
roof not moving

Two criterias met ?

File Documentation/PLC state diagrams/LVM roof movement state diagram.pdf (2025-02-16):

S0

### IDLE

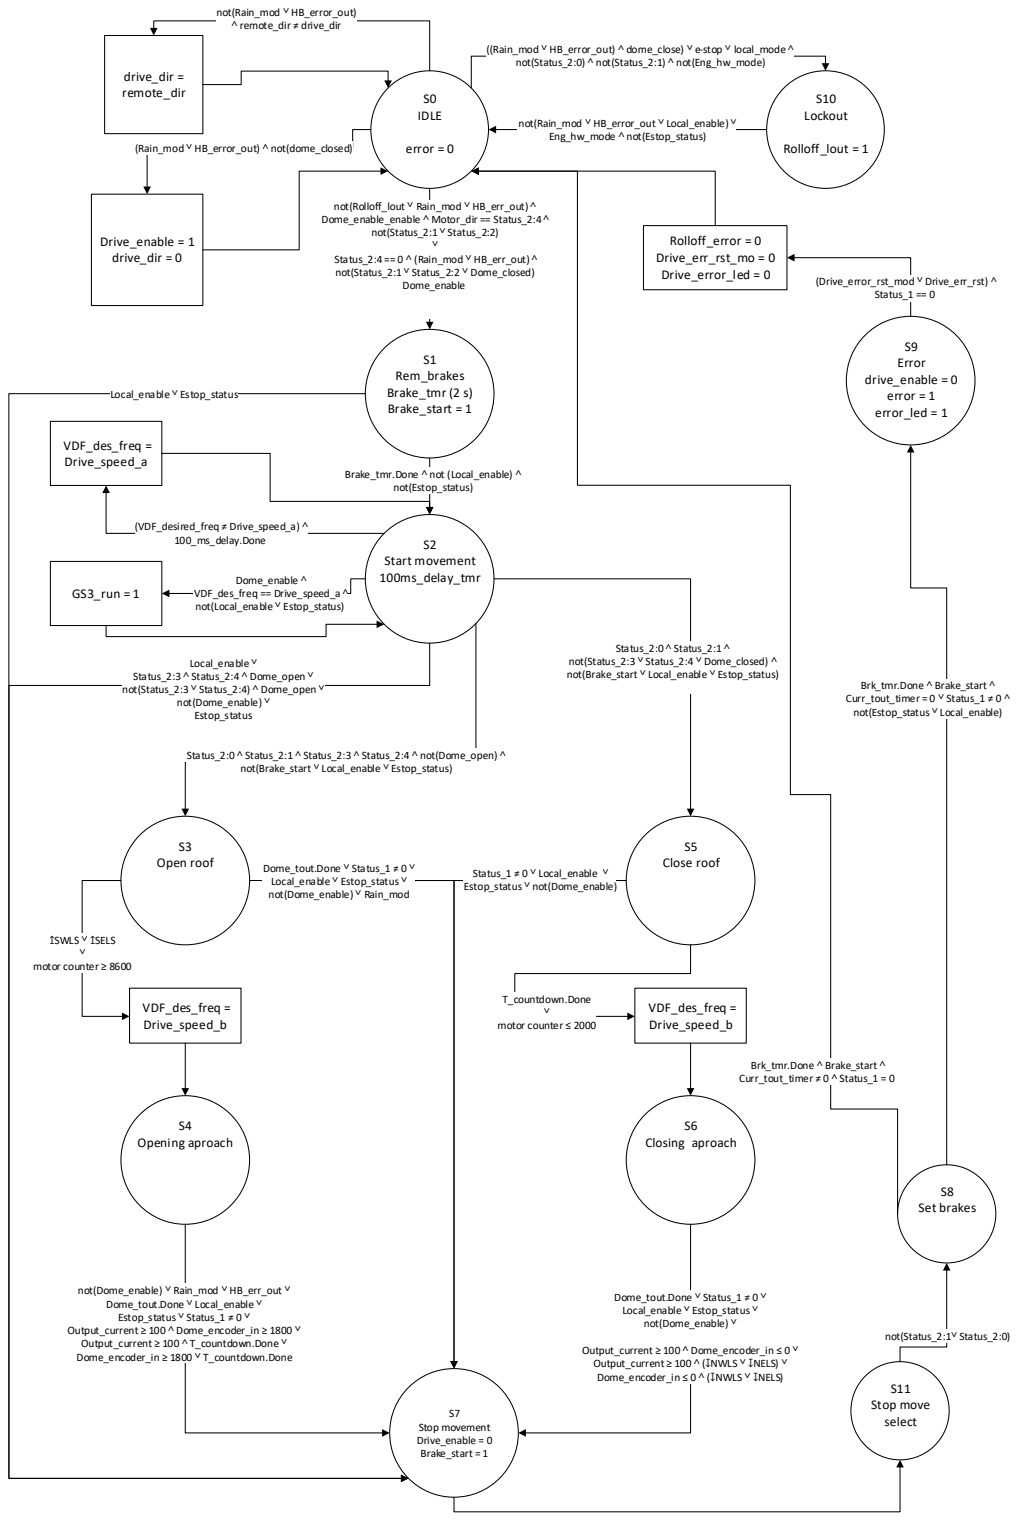
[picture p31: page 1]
not(Rolloff_lout ˅ Rain_mod ˅ HB_err_out) ˄ Dome_enable_enable ˄ Motor_dir == Status_2:4 ˄ not(Status_2:1 ˅ Status_2:2) ˅ Status_2:4 == 0 ˄ (Rain_mod ˅ HB_err_out) ˄ not(Status_2:1 ˅ Status_2:2 ˅ Dome_closed) Dome_enable; error = 0; drive_dir = remote_dir; not(Rain_mod ˅ HB_error_out) ˄ remote_dir ≠ drive_dir; (Rain_mod ˅ HB_error_out) ˄ not(dome_closed); Drive_enable = 1 drive_dir = 0; S10 Lockout; Rolloff_lout = 1; not(Rain_mod ˅ HB_error_out ˅ Local_enable) ˅ Eng_hw_mode ˄ not(Estop_status)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

((Rain_mod ˅ HB_error_out) ˄ dome_close) ˅ e-stop ˅ local_mode ˄
not(Status_2:0) ˄ not(Status_2:1) ˄ not(Eng_hw_mode)

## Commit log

2021-11-15 Initial commit of the LVM PLC enclosure code.
    This commit has the lights and interlock system coded and tested.
    The documentation folder contains state diagrams and a variable spreadsheet.
    [LVM_enc_EXPORT_CMORE.csv, PLC variables.xlsx]
2021-11-24 Rewrote variables for different elements. Add Modbus variables for several inputs & output. Add 2 random variables for hvac testing.
    [LVM_enc_EXPORT_CMORE.csv, PLC variables.xlsx]
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2022-01-04 Fixed plc drive simulator issues & add drive counter variable MHR150 to modbus
    [LVM_enc_EXPORT_CMORE.csv, PLC variables.xlsx]
2022-01-10 Fixed Modbus declaration issue for the dome variables. System is now accepting remote commands.
    [LVM_enc_EXPORT_CMORE.csv, PLC variables.xlsx]
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2023-04-13 2023 04 13 First version on Enclosure
    System was installed on Enclosure, IP was configured and connection tested.
    [LVM_enc_EXPORT_CMORE.csv]
2023-04-14 Update excel file with new GS3 monitored variables. - Monitor status 2. - Frequency set point. - Output Frequency. - Output Current.
    [PLC variables.xlsx]
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2023-04-20 Working Enclosure control through overcurrent
    First deployed version of the enclosure system.
    This version controls the motor drive through RS-485 and Modbus RTU.
    Limits controlled by overcurrent / timeout / drive bit.
    [LVM Simple_EXPORT_CMORE.csv]
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2023-04-20 Updated the ladder logic to include the errors as cause to jump stage S2 -> S0
    [LVM Simple_EXPORT_CMORE.csv]
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2023-08-30 Add remote roll off white light control
    - Connected current sensors on roll-off light circuits.
    - MC245: Bright (white) lights status.
    - MC246: Night (red) lights status.
    - Connected roll off white lights relay.
    - Set coil to 1 to change relay state.
    - MC239: Toggle bit.
    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
    [LVM Simple_EXPORT_CMORE.csv]
2023-08-30 Add Platform red light remote switch
    Add platform red light remote switch to PLC
    - Toggle variable is MC240.
    - Read Variable is MC246.
    [LVM Simple_EXPORT_CMORE.csv]
2023-08-30 Work was done over an older version.
    Merged both versions together to get to the newest PLC code.
    [LVM Simple_EXPORT_CMORE.csv]
2023-10-27 Add heartbeat subprogram.
    Two versions of heartbeat subroutines were implemented.
    - Time based
    - Wait 5 minutes before calling the connection out.
    - Count based
    - Wait three times system didn't get response from the servers to call the connection out.
    Once the connection is called out, roll-off is closed.
    [HVAC Modbus configuration.xlsx, LVM Simple_EXPORT_CMORE.csv, PLC variables.xlsx]
2023-10-27 Add roll-off status.
    Add roll-off status
    - MC1006: Dome closed.
    - MC1007: Dome open.
    Add HVAC output at Y8, it is under test.
    [LVM Simple_EXPORT_CMORE.csv, PLC variables.xlsx]
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2024-01-16 Add Subsystems to PLC
    - PLC heartbeat
    - Send email to lvm-critical after 180 seconds of lost communication with LVM servers.
    - Lights.
    - Add main panel lights & current sensors.
    - Limit switches.
    - Activate west side limit switches.
    [LVM Simple_EXPORT_CMORE.csv]
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2024-01-17 Add engineering features for hardware and software
    Add variables MC900 and 901
    - MC900 Hardware engineering mode: Bypasses all hardware security measures (Disable local mode).
    - MC901 Software engineering mode: Bypasses all software security measures (Emails disabled).
    [LVM Simple_EXPORT_CMORE.csv]
2024-01-17 Heartbeat activated
    PLC/server heartbeat was activated. PLC will automatically close the dome when communication has been lost more than three minutes
    [LVM Simple_EXPORT_CMORE.csv]
2024-06-09 Changed roll-off limit switch code
    Now the limit switches are located near the north wall, therefore, it has more accurate actuation.
    [LVM Simple_EXPORT_CMORE.csv]
2024-06-09 Fixed bug in the roll-off direction
    Fixed issue on the roll-off direction.
    It was possible to send a change of direction command from the ECP, which wasn't passed to the GS3.
    [LVM Simple_EXPORT_CMORE.csv]
2024-06-24 Add Rain sensor to PLC
    Add rain sensor to PLC
    Rain sensor output is in MC 7000
    Rain counter (how many times has it activated) is MHR700
    Drive code wasn't updated, to prevent false positives.
    [LVM Simple_EXPORT_CMORE.csv]
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2024-07-09 Motor encoder added as input
    Motor encoder enabled as input
    MHR150 has the encoders raw count.
    MHR151 has the theoretical distance moved by the chain in mm.
    MHR152 has the measured gap off the roof in mm.
    [LVM Simple_EXPORT_CMORE.csv, PLC variables.xlsx]
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2024-08-14 Prepare code to roll off control redesign
    [LVM enclosure_EXPORT_CMORE.csv]
2024-08-16 New drive logic
    This branch sets the path to the new roll-off-motion logic.
    It uses all available sensor.
    For now, motor brakes are skipped, but are included in the code.
    [LVM enclosure_EXPORT_CMORE.csv, PLC variables.xlsx]
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2024-08-16 Prepare code for field tests.
    Add variables for field test on the roof.
    Add static variables for timers and a constant to select the logic that is going to be used.
    [LVM enclosure_EXPORT_CMORE.csv]
2024-09-03 Corrected the roll off roof logic
    While commissioning the new roll off roof logic, I found several bugs in my code, which were patched.
    Updated state & flow diagrams will be updated later.
    [LVM enclosure_EXPORT_CMORE.csv]
2024-09-27 V0.9
    New logic code tested under José's stress tests.
    Will be merged to master
    [LVM enclosure_EXPORT_CMORE.csv]
2024-10-27 Version 0.91
    - Changed Status 2 variable from MHR1024 to MHR412
    - Status 2 was read two times from GS3, do to old engineering test.
    - Moving read variable from MHR1024 to MHR412, simplifies the GS3 reading schema.
    - Add SNTP synchronization.
    - Found system clock two minutes ahead of time.
    - Add SNTP synchronization at the first scan and every day at local noon.
    - Synchronization server is the Chilean official time server (ntp.shoa.cl).
    - Named and added information to variables.
    - Fixed rain modbus timer unit.
    - It was set wrongly to ms instead of seconds.
    [LVM enclosure_EXPORT_CMORE.csv]
2024-11-21 V0.92
    Fixed issue with roll-off state machine, where the state of the LS was read instead of the flank.
    [LVM enclosure_EXPORT_CMORE.csv, PLC variables.xlsx]
2024-12-31 Fixed enclosure logic
    Changed way enclosure limits parameters are triggered, preventing the system from jumping stages when a bogus signal is detected
    [LVM enclosure_EXPORT_CMORE.csv]
2024-12-31 V0.93
    First commit to implement ECO-2204-11-20b.
    Repurposed old Drive block (deprecated) to run the overcurrent only mode.
    Mode selection is done by modbus coil 99.
    After MC99 is changed to 1, dome_enable (MC100) will trigger the closure.
    It works only in closure mode, therefore it is not necesary to give the PLC the dome direction (MC102)
    [LVM enclosure_EXPORT_CMORE.csv]
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2025-01-31 Adjust several limit values
    - Adjust several limit values in the code.
    - Add internet access bit, to prevent the e-mail spamming when internet is down.
    - Update the PLC variables spreadsheet.
    [LVM enclosure_EXPORT_CMORE.csv, PLC variables.xlsx]
2025-02-01 Changed local variable logging
    New data package is:
    MC1 MC2 MC3 MC99 MC100 MC101 MC102 MC103 MC105 MC106 MC107 MC108 MC109 MC110 MC111 MC112 MC200 MC201 MC202 MC235 MC236 MC237 MC238 MC239 MC240 MC335 MC336 MC337 MC338 MC339 MC340 MC600 MC601 MC602 MC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
    For variable definition please refer to PLC variables.xlsx in the documentation folder.
    [LVM enclosure_EXPORT_CMORE.csv]
2025-02-01 Update documentation
    Update the PLC variables.xlsx and add a roll-off timing spreadsheet
    [PLC variables.xlsx, Roll-off timmings.xlsx]
2025-02-13 Operational version as of the third of February
    Reviewed the dome code
    - Delete logic that would be never met.
    - Checked timeouts after fixing the encoder issue on the motor side.
    Fixed issues with the heartbeat e-mail deliveries.
    - If internet access is down, no e-mails will be sent.
2025-02-16 Last update post documentation
    Last PLC update after documentation, Found minor bugs while documenting in the overcurrent mode. System checked.
    [LVM enclosure_EXPORT_CMORE.csv]
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2025-05-09 Spectrograph room estop
    Patricio Jones added the new estop buttons from the spectrograph room.
    [LVM enclosure_EXPORT_CMORE.csv]
2025-05-13 Add new PLC power supply schematic
    Add new double power input power supply schematic.
    Updated LVM enclosure PLC main schematic.
    [PLC dual power input.SchDoc]
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
